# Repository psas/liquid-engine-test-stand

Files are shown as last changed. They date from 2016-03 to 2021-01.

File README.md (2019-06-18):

# liquid-engine-test-stand

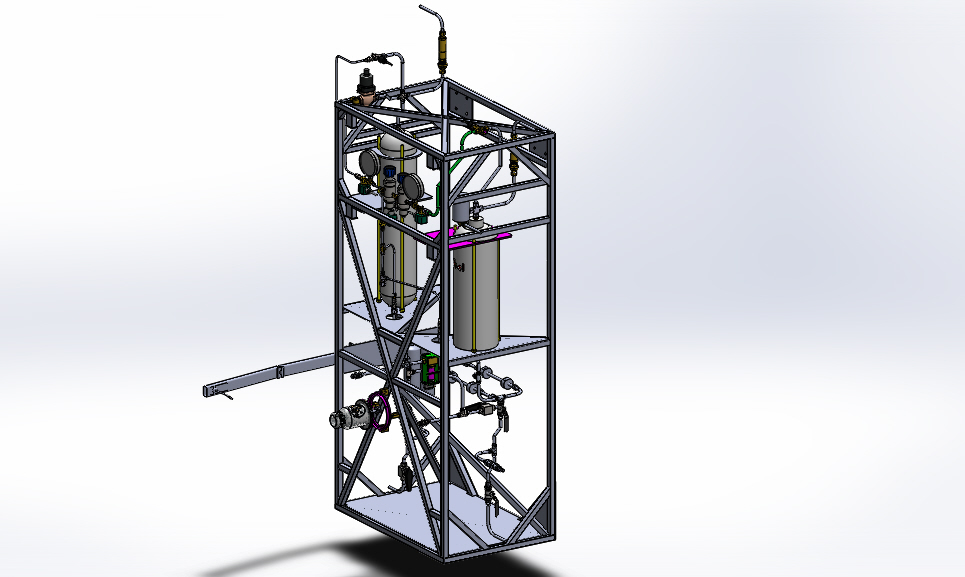
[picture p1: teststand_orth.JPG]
Orthographic View of Test Stand


# Liquid Fuel Engine Test Stand (LFETS) Project Overview

  PSAS team members have already designed and built a [2.5 kN regeneratively cooled bipropellant (liquid oxygen and ethanol) rocket engine](https://github.com/psas/liquid-engine-capstone-2015). This engine design included a number of innovative features including fully parametric CAD design using python scripts and SolidWorks, direct metal laser sintering (DMLS) additive manufacturing by i3D manufacturing, direct spark ignition and pintle injection. Although the rocket engine itself has already been produced, much of the overall system complexity lies in the piping, control, and data acquisition systems which support it. This project intends to flesh out these systems in order to test the engine and its successors.

  The test stand will safely test current and PSAS future generation liquid fuel engines prior to integration into a flight vehicle. PSAS will use the stand to measure engine performance, liquid fuel and oxidizer flow rates, propellant mixing capabilities and other engine performance figures of merit. These tests will be performed remotely, using automated valve switching and data acquisition systems. The LFETS system is designed to be portable by truck, and will support propulsion testing of engines up to 10 kN of thrust. The project will be open-source and will utilize live web-based Jupyter notebook design documentation.

  The feed system uses a classic regulated pressure-fed thermodynamic cycle. Gaseous nitrogen is the pressurant. The LFETS system includes a welded thrust loading truss structure, propellant and pressurant supply tanks, and feed system flow componentry. The project also includes safety and Failure Mode Effects Analysis, and procedures for safe operation and transport.
The LFETS Electrical Ground Support Equipment (EGSE) will allow for the test stand to be controlled remotely. The test stand computer controls all actuators in the LFETS system, auto-sequences engine ignition, start, shutdown, pad-safing, and contingency procedures for any test exception, as well as receiving telemetry from sensors and instrumentation. The LFETS EGSE system is derived from the 3rd generation [PSAS launch tower computer](https://github.com/psas/launch-tower), which uses a BeagleBone Black microcontroller, the [Marionette open-source DAQ](https://marionette-daq.github.io/), and a custom “SCADA-like” GUI.

## Useful Links

[CAD Files](https://github.com/psas/liquid-engine-test-stand/tree/master/cad/Test%20Stand%20CAD%20Files/current%20assembly)

[CAD Guide](https://github.com/psas/liquid-engine-test-stand/blob/master/cad/CAD%20Guide.pdf)

[Bill of Materials](https://drive.google.com/open?id=1SeBntyje6zpfy1jSxysdBP59IyhFcIg6SvVT6w5Bf4Y)

[PID](https://github.com/psas/liquid-engine-test-stand/tree/master/PID)

[Capstone Class Work](https://github.com/psas/liquid-engine-test-stand/tree/master/2018-2019%20Capstone%20documentation/Class%20papers%20and%20presentations)

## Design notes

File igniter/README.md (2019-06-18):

# Igniter for 2.2 kN Liquid Engine

Calculations have been acquired by inspecting the [2015 Liquid Engine Captsone](https://github.com/psas/liquid-engine-capstone-2015/blob/master/2kN/analysis/Jupyter_Notebooks/LFRE.ipynb)

Methods have been refined by interpretation of documents in the external_resources/ directory.

## UPDATES FROM 2019 CAPSTONE:

Igniter design documentation and validation can be found in the root folder under [Igniter-Design-Documentation.pdf](https://github.com/psas/liquid-engine-test-stand/blob/master/igniter/Igniter-Design-Documentation.pdf)  I would recommend starting with this document.

CAD for igniter arm can be found in the [Igniter Mockup CAD](https://github.com/psas/liquid-engine-test-stand/tree/master/igniter/Igniter%20Mockup%20CAD) folder.  The main assembly for the mockup is "Main Assembly.sldasm"

Momentum calculations for holding the arm in place can be found in the [calculations folder](https://github.com/psas/liquid-engine-test-stand/tree/master/igniter/Calcuations).

New Igniter BOM can be found in the PSAS Shared Drive, in the main [LFETS BOM](https://docs.google.com/spreadsheets/d/1SeBntyje6zpfy1jSxysdBP59IyhFcIg6SvVT6w5Bf4Y/edit?usp=sharing) document.

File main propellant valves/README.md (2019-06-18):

# Main Fuel and LOX Valves

The main pressurant valves consist of the main fuel valve and the main oxidizer valves.  The valves are control the flow of the Fuel and Oxidizer between the propellant tanks and the engine. The main fuel valve will be located on the fuel side of the test stand which carries Isopropyl alcohol. The main oxidizer valve will be located on the oxidizer side of the test stand which carries liquid oxygen.  The design requirements for each valve is that they be actuated remotely and able to work at pressures up to ~1000 psi. The LOX valve must also be able to work at cryogenic temperatures and be LOX compatible.

Several iterations of the main propellant valves have been worked on.

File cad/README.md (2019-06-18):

# Liquid Engine Test Stand CAD

  This section contains all the CAD models from previous and current version of the test stand made using Solidworks.
  
 ## Current Assembly
 
  This folder contains all the models for the current version of the test stand. The assembly for the test stand is labled LMTS_5. 
  
  Note: the entire folder must be downloaded in order to open the test stand assembly to load with all its components.
 
 ## Documentation
 
  ### CAD Guide
  
  This document contain information on all revisions, process, findings, and recommendations pertaining to constructing the test stand.
  
  ### Pipe Orders
  
  This folder contains folders and zip files that contain CAD drawings of pipes that have been or will be sent out for manufacturing.
  
 ## Previous Versions (from oldest to most recent)
 
  These folders contain previous versions of the test stand
  
  V.1
  test_stand_mods
  2016

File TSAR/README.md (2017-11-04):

# TSAR
Test Stand Automation and Regulation system for the Portland State Aerospace Society's (PSAS) Liquid fuel engine test stand.

## New Member Onboarding

If you are interested in joining the TSAR team, please reference 'Onboarding.pdf' in the root of this repository. 

## Definitions

LFETS - Liquid fuel engine test stand

Module - Valves, sensors, the engine, the igniter. Anything that is a single moving, sensing or functional unit.

## Test Stand Automation and Regulation System Overview

The TSAR group will build an embedded controls and data acquisition system (CDAQ) for a liquid fuel rocket engine test stand for the Portland State Aerospace Society. Solving this issue is vital because developing a liquid fuel rocket engine will decrease PSAS’s cost per launch drastically while also opening the door for considerably higher peak apogees. Without the development of a safe CDAQ solution for the test stand, PSAS cannot reach its goals. The TSAR solution is a student led, in house solution which will create a custom taylored, safety oriented soluton for test stand CDAQ. Our solution is unique because it will be entirely open-sourced with a focus on repeatability and simplicity to allow other amateur rocket groups to benefit from the liquid rocket engine technology. We will use an off-the-shelf Beagle Bone Black embedded computer and a Marionette DAQ board (a former PSU capstone) to implement this system and all software will be developed by the TSAR team of PSU undergraduates.

Project Contact: Mark Musil - Junior in Electrical Engineering at Portland State University (mmusil@pdx.edu)

## Key Requirements

The following aspects of the system are mandatory. More details are present in the document 'TSAR_Requirements.docx' in the root of this repository. The core features are:

1. Interactive graphical dashboard for state control
2. Safety and security of the entire system
3. Clean, thorough documentation of all group efforts including well-commented code, photographic and videographic artifacts, and thorough usage and debugging resources. 

#### What are the major deliverables?
A graphical front end with safety features. A nervous system of sensors and actuators with realtime data output from the RPi3 to the front-end.

#### How will we get to those deliverables and the deadline?

Divison of the project into: 

High level application design - GUI, interactive LFETS diagram, state control, security features, real-time data output, data storage

Mid-level system architecture - Discretization of the firing sequence into states, designation of states for each module.

Low-Level sensor specification and sensing - Specification of each sensor's range, and performance characteristics and interfacing of the sensors and actuatuators with the marionette/Rpi3.

#### What are the milestones we need to hit?
October: assessment of each High,mid,low system requirements and the tools which will be used for each system.
November: Completed state-machine design, Front end specifications completed, sensor specifications completed.
December: Interface with the fuel sensor or other LFETS needs and provide data output for their project.
January: All sensors specified, all valves under control.
February: Interface with all sensors and have real-time, time alligned data output.
March: 
April:
May: Hot fire :)
#### Are there dependencies that could impact the timeline?

It is important that we allign with the needs of the test stand team's needs. In addition, we need to begin delivering a part's list to the Beta project people. 

## Critical Objectives in Temporal Order (To-do list)

1. ### Pre-design
	1. Team Orientation
		1. General Training
			- [] GitHub
			- [] Python Notebook
			- [] System Overview
	2. Task Distribution
		1. Sensor Acquisition and Interfacing
		2. Actuator Acquisiton and Interfacing 
		3. Beagle Bone Black to Actuators
		4. Marionette To sensors
		5. System Design 
		6. Front-End and GUI
		7. Networking
		8. Record Keeping and Documentation
2. ### Design Stage
	1. Consult with Doug Hall concerning System Design
	2. Meet with Jacob Tiller about sensor requirements
	3. Investigate tools such as PyQT
	4. Brainstorm
	5. Determine Critical Path
3. ### Prototyping Stage 1
	1. Develop skeletal prototype of each sub system
		1. Minimal working set for interfacing
	2. Build sensor to screen prototype.

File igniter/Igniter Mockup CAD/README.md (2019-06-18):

# CAD guide

The top level assembly is "Main Assembly.sldasm"

The hinges on the igniter arm segments have changed a bit in the physical design, so as to minimize play.

This cad is mainly to be used as a mockup - not everything about the design is canon.

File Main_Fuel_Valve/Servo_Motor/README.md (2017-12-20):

# Main Fuel Valve

Servo Actuated Ball Valve

## To do:
  
  - [x] Design housing for servo, linkage, and valve
      - [x] Must maintain motor and valve-housing position against torque during action
        
      - [x] Must have sufficient clearance for physical linkage
      - [x] Print V.0 housing and test
     - [x] Make necessary updates for V.1 
        - [x] Print updated housing
        - [x] Post-process housing for assembly
    - [x] Acquire hardware & bits
    - [x] Assemble
- [x] Write Arduino code for pressure test
 - [ ] Acquire battery with sufficient amperage to operate valve
- [ ] Create test plan
        - [ ] determine all needed parts
        - [ ] acquire all needed parts
- [ ] Test valve with water at 1000 psi

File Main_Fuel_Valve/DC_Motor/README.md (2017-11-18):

# 12VDC Motor controlled Main Fuel Valve
<p align="center">
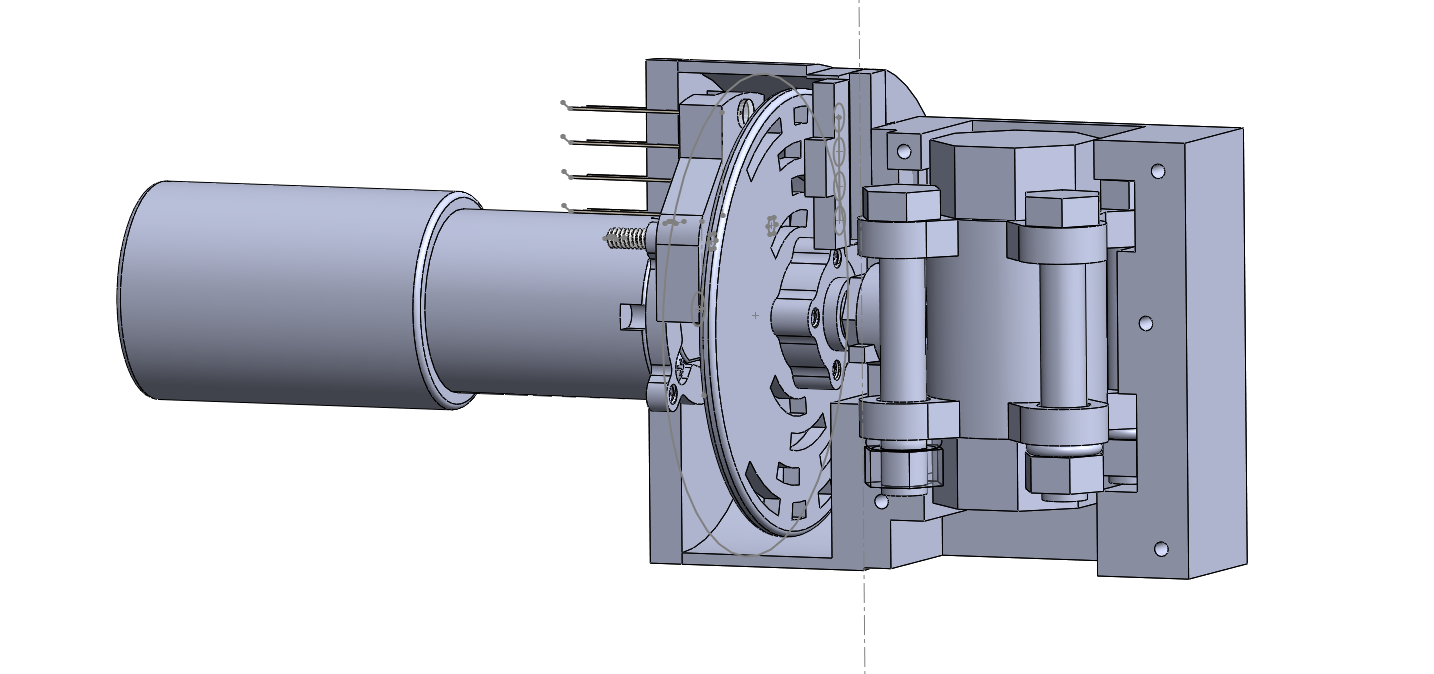
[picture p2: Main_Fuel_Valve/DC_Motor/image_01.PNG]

</p>

 DC Motor Valve control overview

   The 12VDC Motor Control project uses a very high torque planetary geared DC motor to crack, open, and close the main fuel valve. To control the position of the valve, a rotary encoding disk allows photo-sensors to receive light through concentric holes in the disk. The holes are designed to position the valve at shutoff, cracked from 0 to +60 degrees in 5 degree increments, and full open. The device is currently being controlled by an arduino.

###

## CAD Models
  
   The main assembly file is 12VDC_valve_assembly.SLDASM  
     
   PSAS authored files are:  
  
   12VDC_valve_assembly.SLDASM  
   Motor_12VDC_638263.SLDPRT - From drawing  
   Motor_12VDC_638263_shaft.SLDPRT - from drawing  
   Sensor_Head.SLDPRT  
   encoding_wheel.SLDPRT  
   Housing-Back.SLDPRT  
   Housing-Front.SLDPRT  

## Control

#### Basic Theory

The device uses Gray Code built into the encoding disk. The scheme is as follows: 

State - Code - Position

  00 - 0000 - detent (all)  
  01 - 0001 - closed  
  02 - 0011 - closed +5 dgrees  
  03 - 0010 - closed +10 degrees  
  04 - 0110 - closed +15 degrees  
  05 - 0111 - closed +20 degrees  
  06 - 0101 - closed +25 degrees  
  07 - 0100 - closed +30 degrees  
  08 - 1100 - closed +35 degrees  
  09 - 1101 - closed +40 degrees  
  10 - 1111 - closed +45 degrees  
  11 - 1110 - closed +50 degrees  
  12 - 1010 - closed +55 degrees  
  13 - 1011 - closed +60 degrees  
  14 - 1001 - Cracked <-> Open  
  15 - 1000 - Open (closed plus 90 degrees)  
  
  Detent position idicates an extreme condition. When a detent condition occurs, the script will determine the corrective action base on desired state.
  
  #### Control profiling
  
  Two control features requiring implementation are **Encoding Disk Interpolation** and **DC Motor Inertia Lag Profile**.
  
  **Encoding DIsk Interpolation**
      The source LED light is sensed by the photo-tranistors as the encoding wheel turns. At times the source LEDs will be partially occluded by the encoding wheel. The voltage throughput of the phototransistors will have a period of ramping up and ramping down due to this partial occlusion as the encoding wheel turns. If these ramping periods are profiled, a state can be identified more accurately than the 5 degree increments of the gray code. If these intermediate states can be proven accurate and reliable the encoding wheel should provide significantly improved resolution.
      
  **DC Motor Intertia Lag Profile**
      Due to the gearing and the inertia of the rotating mass in the motor, the motor continues to turn for a short time after it is switched off. This lag needs to be profiled so a switching point may be automatically determined based on desired state.
  
## To do:
  
  - [x] Design Motor to mount housing using jacob's design for the servo-motor as a base
    - [x] Must maintain motor and valve-housing position against torque during action
    - [x] Must have a mount for the "Sender" LED's (5mm) to provide bright light to the sensors
        - [ ] Bonus: Shield the "sender" and sensor heads from outside sources of light
    - [ ] Print the Housing front, back, LED Sender head, and photosensor head
        - [x] Initial printing of front, back, LED Sender head, and photosensor head
        - [ ] Print updated encoding wheel
        - [ ] Post-process housing front & back
    - [ ] Acquire hardware & bits
    - [ ] Assemble

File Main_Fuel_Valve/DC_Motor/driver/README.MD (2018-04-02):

# Code for the 12VDC motorized encoding valve project for LFETS.
### under construction

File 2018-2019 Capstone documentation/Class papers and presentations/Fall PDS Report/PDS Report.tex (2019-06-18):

% !TEX TS-program = pdflatex
% !TEX encoding = UTF-8 Unicode

% This is a simple template for a LaTeX document using the "article" class.
% See "book", "report", "letter" for other types of document.

\documentclass[11pt]{article} % use larger type; default would be 10pt
%\documentclass[twocolumn, 11pt]{article}  % will give a two column article with larger type
\usepackage{setspace} % lets you set the line spacing to single, 1.5 or double spaced. place after \maketitle
%\singlespace 
%\onehalfspace
%\doublespace

\usepackage[utf8]{inputenc} % set input encoding (not needed with XeLaTeX)

%%% Examples of Article customizations
% These packages are optional, depending whether you want the features they provide.
% See the LaTeX Companion or other references for full information.

%%% PAGE DIMENSIONS
\usepackage{geometry} % to change the page dimensions
\geometry{letterpaper} % or letterpaper (US) or a5paper or....
%\geometry{margin= 1in} % for example, change the margins to 2 inches all round
% \geometry{landscape} % set up the page for landscape
%   read geometry.pdf for detailed page layout information

\usepackage{graphicx} % support the \includegraphics command and options
\usepackage{float}
%\floatstyle{boxed} 
\restylefloat{figure}

%\listoffigures  % will give a list of figures
% \renewcommand{\figurename}{Example}  % changes it from figure to Example

%\usepackage{wrapfig} % will allow use of text wrapping around a figure
%\begin{wrapfigure}[lineheight]{position}[overhang]{width} would be used 
% r, l, i, o (right, left, inside edge, outside edge) (lower case is exactly here, upper case is float. for width use 0.5\textwidth for 1/2 of text width on the page

% \usepackage[parfill]{parskip} % Activate to begin paragraphs with an empty line rather than an indent

%%% PACKAGES
\usepackage{booktabs} % for much better looking tables
\usepackage{array} % for better arrays (eg matrices) in maths
\usepackage{paralist} % very flexible & customisable lists (eg. enumerate/itemize, etc.)
\usepackage{verbatim} % adds environment for commenting out blocks of text & for better verbatim
\usepackage{subfig} % make it possible to include more than one captioned figure/table in a single float
% These packages are all incorporated in the memoir class to one degree or another...

%%% HEADERS & FOOTERS
\usepackage{fancyhdr} % This should be set AFTER setting up the page geometry
\pagestyle{fancy} % options: empty , plain , fancy
\renewcommand{\headrulewidth}{0pt} % Gives a line at the top
\renewcommand{\footrulewidth}{0pt} % gives line at the bottom
\lhead{}\chead{}\rhead{} % puts stuff in the header
\lfoot{}\cfoot{\thepage}\rfoot{} % puts stuff in the footer

% \usepackage{lastpage}      % use this to have a x page of xx
%\cfoot{\thepage\ of \pageref{LastPage}} % this is the command for the center foot

%%% SECTION TITLE APPEARANCE
\usepackage{sectsty}
\allsectionsfont{\sffamily\mdseries\upshape} % (See the fntguide.pdf for font help)
% (This matches ConTeXt defaults)

%%% ToC (table of contents) APPEARANCE
\usepackage[nottoc,notlof,notlot]{tocbibind} % Put the bibliography in the ToC
\usepackage[titles,subfigure]{tocloft} % Alter the style of the Table of Contents
\renewcommand{\cftsecfont}{\rmfamily\mdseries\upshape}
\renewcommand{\cftsecpagefont}{\rmfamily\mdseries\upshape} % No bold!

\usepackage{amsmath} % allows use of \eqref{} to add () around referenced equations

%Outline format 
\renewcommand{\theenumi}{\Roman{enumi}. }
\renewcommand{\labelenumi}{\theenumi}

\renewcommand{\theenumii}{\Alph{enumii}. }
\renewcommand{\labelenumii}{\theenumii}

\renewcommand{\theenumiii}{\roman{enumiii}. }
\renewcommand{\labelenumiii}{\theenumiii}

\renewcommand{\theenumiv}{\alph{enumiv}) }
\renewcommand{\labelenumiv}{\theenumiv}

% Change the font size to something other than 10, 11, or 12 pt
%\usepackage{mathptmx}
%\usepackage{anyfontsize}
%\usepackage{t1enc}

%%% END Article customizations

%%% The "real" document content comes below...

%\title{Report Name} % alternate report title page
%\author{Jacob Tiller}
%\date{} % Activate to display a given date or no date (if empty),
         % otherwise the current date is printed 

\begin{document}
	% \fontsize{14}{16}\selectfont % Change font size, requires packages above
	\begin{titlepage}
		\centering
		%\includegraphics[width=0.15\textwidth]{imagename}\par\vspace{1cm}
		{\scshape\LARGE Product Design Specifications Report
\par}
		\vspace{.6in}
		{\huge\bfseries Liquid Propellant Engine: \par}
		\vspace{.2in}
		{\scshape\Large Test Stand Integration and Testing \par}
		\vspace{.75in}
		{\Large\itshape Bert DeChant \\ Sam Hasting Hauss \\ Peter Mazhnikov \\ Matthew Ng \\ Erik Potenza \\ Eric Thomas \\ Jacob Tiller \par}
		\vfill
		Capstone Adviser:\par
		Mark Weislogel

		\vfill

% Bottom of the page
		{\large \today\par}
\end{titlepage}

%\maketitle  % alternative make title with just author and report name stuff.
%\thispagestyle{fancy} 

\section{Purpose}

This document is intended to act as a guide for the development and testing of the Liquid Propellant Engine Test Stand. The Project Design Specification (PDS) will be used as the meter stick by which to ensure that all customer requirements are met and that the project is on track. 

\section{Project Background}
Portland State Aerospace Society (PSAS) is a collection of students, citizen-engineers and industry mentors with a long history of developing low-cost, open-source rocket hardware and avionics systems. In 2018 PSAS joined the Base 11 Space Challenge (Base 11),  a competition for student university groups to produce and launch a liquid-propelled single stage rocket to 100km. In line with PSAS’ vision statement, the challenge acts as an additional incentive to build and launch the next PSAS launch vehicle, Launch Vehicle 4 (LV4). Prior to the design and construction of LV4, the rocket’s liquid bi-propellant rocket engine must be tested.

PSAS is preparing to test a 2.2 kN regeneratively cooled bipropellant (liquid oxygen and isopropanol) rocket engine. This engine design has a number of innovative features including fully parametric CAD design using Python and SolidWorks, direct metal laser sintering (DMLS) production by i3D manufacturing, augmented spark torch ignition and pintle injection.

The Liquid Propellent Engine Test Stand was originally produced by a Portland State University capstone team in 2015. The team designed, analyzed, and constructed the frame of the test stand and set in path many of the construction elements. Since the frame was constructed, the stand has been awaiting final integration and installation of some subsystems including propellant and cryogenic plumbing as well as the engine mounting \& interfacing. 

PSAS has asked our team to complete the construction of the test stand and test the 2.2kN engine. Upon completion, the test stand will continue to serve the organization by testing the liquid-oxygen electric feed system, cryogenic composite oxidizer and propellant tanks, and the next generation 8kN rocket engine. Our work will synergize with the efforts of previous capstone teams to prototype the technology for LV4 and to compete in the Base 11 Space Challenge.

\section{Mission Statement}
The proposed project is to integrate, test, and analyze our prototype engine.  An analysis of the first static test fire is scheduled to be accomplished in the spring of 2019.

We will integrate and test the previously designed engine and validate its performance metrics including thrust, cooling capabilities, and chamber pressures. Engine testing will be conducted in a reproducible manner according to a written standard operating procedure which will emphasize safe operation. Other procedures for interacting with authorities, safety, and testing site hazard analysis will be written and used during this project. The captured data from the static fires and the analysis methods will be published under an open-source license.

The test stand needs to stand up to the rigors of testing a rocket engine while also incorporating safety and data acquisition capabilities.  Furthermore, it needs to have the ability to be used with multiple sizes of engines, although only the 2.2kN engine will be tested in the Spring of 2019.

An analysis will be conducted to determine engine performance. Data will be acquired through a Data Acquisition system (DAQ) working under the Test Stand Automation \& Regulation system (TSAR). TSAR will act primarily as a safety and management tool to provide safeguards for both human and system operations.  Upon completion of initial testing, the data acquired will be compared against the engine’s theoretical performance characteristics. Analysis tools include Solidworks, Python programs such as Jupyter Notebooks, and GitHub for collaboration. The data analysis will determine the viability of testing the future generation 8kN engine. The analysis will also prepare PSAS for integration of the liquid engine into the flight-ready control system of future rocket designs to be used in the Base 11 Challenge.

Standard Operating Procedures will be formalized to meet or exceed industry standards as to mitigate risk towards personnel, equipment, and property. All documentation will be created in accordance with relevant industry standards and best practices determined useful by PSAS. All documentation will contain sufficient detail, background information, and operational description to enable a smooth transfer of knowledge to new project members.

\section{Top Level Project Plan}

Project completion will include integration, testing, and analysis of the 2.2kN engine. The project outcomes will be an analysis of the first static test fire, which is scheduled to be accomplished in the spring of 2019, along with the other project deliverables listed below:

\begin{itemize}
\item Post-processing 3D printed engine
\item Jig creation, precision machining, and CT scanning analysis
\item Integrated assembly (including structures, electronic ground support equipment, and plumbing)
\item Control and data acquisition software and design documentation
\item Operational, and transport procedures
\item Failure Effects Mode Analysis (FMEA), House of quality, and system safety analysis
\item Leak, hydro, and system proof testing buy-offs
\item Integrated cold-flow test data, including the engine injector
\item Hot fire test data for the 1.0 version 3D printed engine
\end{itemize}

\begin{figure}[H] % h - place here; t - top of page; b - bottom; p - put on floats only page; ! override parameters, H - place exactly here
\centering
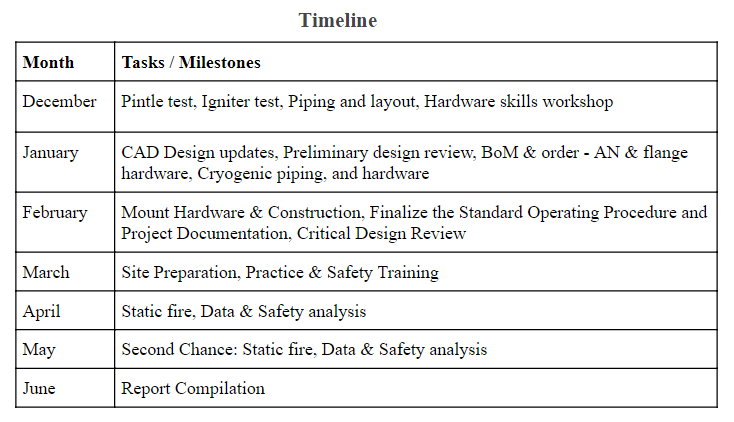
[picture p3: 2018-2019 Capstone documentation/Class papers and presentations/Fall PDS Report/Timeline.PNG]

\caption{Project Timeline \label{fig:timeline}}
\end{figure}

\section{Customers and Stakeholders}

Portland State Aerospace Society - Andrew Greenberg
Capstone Advisor - Mark Weislogel
Capstone Class - Sung Yi / Faryar  
Base 11
Oregon Space Grant Consortium - Catherine Lanier 

\subsection{Customer Interviews and Feedback}

Customer feedback per project customer. 
The main bullet is the project customer and the sub-bullets are the requirements. 

\textit{PSAS:}
Interview Question: What kind of documentation do we need?
\begin{itemize}
\item Create a formal failure mode and effect analysis document
\item Create a Standard Operating Procedure Manual
\item Create a post-firing analysis of engine with suggestions
\item Create a background, research, and theory of operation document
\item Create training materials
\item Create documents for system maintenance
\item Create documents for test site management
\item Create documents for the transportation of the test stand and propellants
\item Create a SolidWorks CAD model of test stand assembly
\item Regularly send all technical documents and files to Github
\item All other tests stand administrative files to be stored on PSAS shared google drive
\item Create a bill of materials
\end{itemize}

Interview Question: What safety standards must be met?
\begin{itemize}
\item Safety procedures are known and followed
\item Participation in any mandatory safety training
\item Human interaction withstand during test must be minimized
\item No person(s) is to approach the test stand while the system is pressurized
\item Redundant systems must be implemented to prevent accidental pressurization of the system
\end{itemize}

Interview Question: What will be needed for the system?
\begin{itemize}
\item Isopropyl alcohol will be the fuel
\item Liquid oxygen will be the oxidizer
\item Nitrogen gas will be the pressurant
\item Data acquisition equipment from TSAR
\item 2.2 kN engine from PSAS
\item Fully constructed test stand
\end{itemize}

Interview Question: What data will we need to acquire?
\begin{itemize}
\item Engine chamber pressure
\item Fuel mass flow rate
\item Propellant mass flow rate
\item Injector spray angle
\end{itemize}

\textit{Capstone Adviser:}
Interview Question: What are your goals for meetings?
\begin{itemize}
\item Bi-weekly meetings to discuss project and progress
\end{itemize}

\textit{Capstone Class:}
Interview Question: What documents must be submitted?
\begin{itemize}
\item Create a Project design specification report
\end{itemize}

\section{Product Design Specifications (PDS)}

\begin{figure}[H] % h - place here; t - top of page; b - bottom; p - put on floats only page; ! override parameters, H - place exactly here
\centering
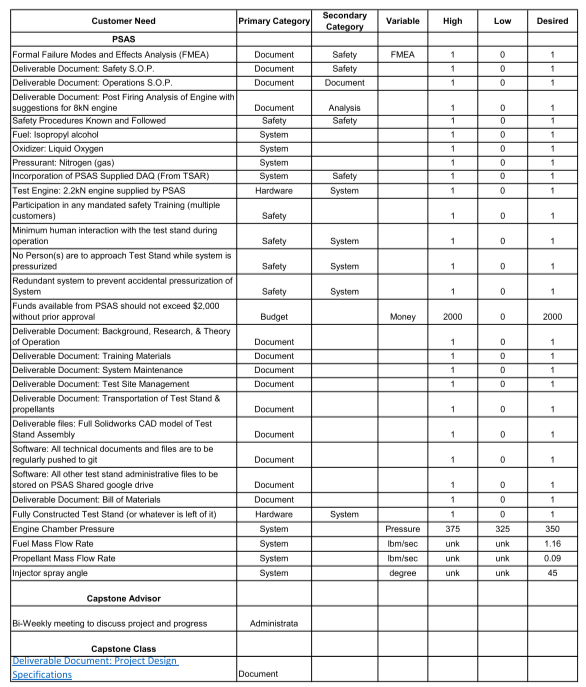
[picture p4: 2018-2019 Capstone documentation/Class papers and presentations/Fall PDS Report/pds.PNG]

\caption{Project Design Specifications \label{fig:PDS}}
\end{figure}

\section{House of Quality}

\begin{figure}[H] % h - place here; t - top of page; b - bottom; p - put on floats only page; ! override parameters, H - place exactly here
\centering
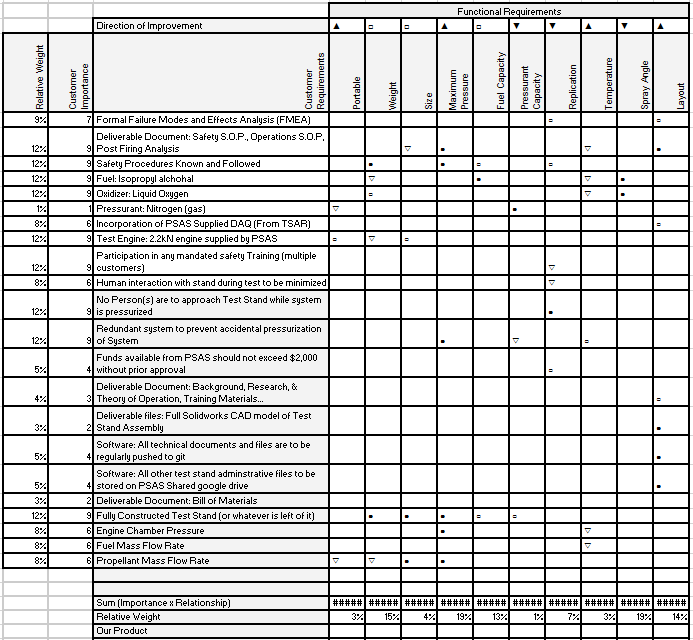
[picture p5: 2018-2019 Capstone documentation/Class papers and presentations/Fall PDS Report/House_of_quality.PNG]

\caption{House of Quality \label{fig:PDS}}
\end{figure}

\section{Conclusion}

A 2.2kN engine supplied by the Portland State Aerospace Society is to be tested using the Liquid Propellant Engine Test Stand. The capstone team is tasked with the integration of some subsystems and components including the engine into the test stand. The team is further tasked with executing a static fire of the stand to acquire engine performance data.

The most important requirements of this project are those related to safety. The team expects to apply significant effort in the creation, practice, and delivery of safety documentation. PSAS requires the highest level of safety and care to be maintained through all phases of integration and operation.

A particularly difficult requirement is the minimization of human interaction. Fuel and oxidizer loading will have minimum human interaction with the test stand. Implementing computerized systems will be an educational experience for the team. It may pose a hurdle as the team has little to no experience with robotic systems.

The team is excited to learn from the integration and static firing of the engine. We anticipate several hurdles in this project but are excited to meet challenges with creative designs and to meet the requirements of PSAS and MCECS Capstone.

\end{document}

%[appendix]
%\appendix
%\clearpage
%\pagenumbering{roman}
%\section{Appendix}

% [Helpful stuff]
%\newpage
%\section{}
%\subsection{}
%\subsubsection{}
%\paragraph{}
%\subparagraph{}

% [Text sizes] 
%{\tiny tiny words} tiny words
%{\scriptsize scriptsize words} scriptsize words
%{\footnotesize footnotesize words} footnotesize words
%{\small small words} small words
%{\normalsize normalsize words} normalsize words
%{\large large words} large words
%{\Large Large words} Large words
%{\LARGE LARGE words} LARGE words
%{\huge huge words} huge words

%[Test styles]
%\textit{words in italics} words in italics
%\textsl{words slanted} words slanted
%\textsc{words in smallcaps} words in smallcaps
%\textbf{words in bold} words in bold
%\texttt{words in teletype} words in teletype
%\textsf{sans serif words} sans serif words
%\textrm{roman words} roman words
%\underline{underlined words} underlined words

% [Lists]
%\begin{enumerate}
%\item First thing
%\item Second thing
%\begin{itemize}
%\item A sub-thing
%\item Another sub-thing
%\end{itemize}
%\item Third thing
%\end{enumerate}

% [Figures and Tables]
% [website for floats and captions]
% https://en.wikibooks.org/wiki/LaTeX/Floats,_Figures_and_Captions 

%\begin{figure}[placement specifier] % h - place here; t - top of page; b - bottom; p - put on floats only page; ! override parameters, H - place exactly here
%\centering
%\includegraphics[width=0.5\textwidth]{filename}
%\caption{ text here \label{fig:marker}}
%\end{figure}

%figure~\ref{fig:marker}

%\begin{table}
%  \centering
%    \begin{tabular}{| l c r |}
%    \hline
%    1 & 2 & 3 \\
%    4 & 5 & 6 \\
%    7 & 8 & 9 \\
%    \hline
%\cline{1-2} column#-column#
%\cline{2-3} column#-column#
%    \end{tabular}
%  \caption{A simple table \label{tab:marker}}
%\end{table}

%table~\ref{tab:marker}

%\begin{equation} \label{eq:marker}
% equation
%\end{equation}

%\eqref{eq:marker}

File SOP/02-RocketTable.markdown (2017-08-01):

---
title: SSH In to Flight Computer Test
layout: base
---

# Rocket table setup

## Common Setup
Start with the Avionics Stack on the rocket cart and batteries charged

 1. Make sure there is something attached to the wifi radio connector (SMA at the top of the Avionics Stack)
    - Either the antenna or a load
 1. Plug in table
 1. Turn on LTC Power brick
 1. Switch on launch tower computer main power
    - Wait a few seconds, verify lights: four reds, blinking blue, blinking green
 1. Visually verify umbilical cord is plugged into the avionics module

## Connect to wifi

 1. Turn on ground control router
 1. Connect to `psas` wifi network
    - Password will be written on the AP or the table

## Verify LTC

 1. `ping ltc`
    - `ltc` should be in the DNS offered via DHCP

## Get flight computer going

 1. Power on Avionics Stack
    - On off switch on battery cable
 1. `ping 10.10.10.5`
    - Actually talking to the RocketNet Hub
 1. Connect to [commander](https://github.com/psas/commander) running on the nuc from  your laptop.
    - Open a browser to <http://ground.psas.lan:5000/>

## In commander
 1. RNH tab -> click "[1] FC On"
    - Click only this, nothing else!
    - Wait for flight computer to boot and establish networking (about 40 seconds? ping 10.10.10.10)
 1. Boot up other services
    - Do *NOT* click "[6] Wifi PA On"
    - Click other on buttons and verify blinky lights for each board
    - You can turn on RasPiCam 2, but the camera is attached to the air frame so it may be a little dull.
 1. Default tab
    - Verify versions of major subsystems by clicking on each button under the "Versions" header

## At laptop
 1. `ssh root@10.10.10.10`
    - Actually talking to Flight Computer
    - See note on wood base of avionics stack for password

## Turning on the RasPiCams
 1. Still on the RNH tab -> click "[2] RasPiCam 1 On"
    - Verify the bottom-most green board starts blinking yellow and green
    - `ping 10.10.10.50` or `ping 10.10.10.60`
 1. `ssh pi@10.10.10.50` or `ssh pi@10.10.10.60` based on which RasPi you're trying to get to
    - Use the usual password

## Common Shutdown
 1. Cleanly shut down the Flight Computer
    - `shutdown now`
    - Wait for FC to shut down (about 30 seconds?  Or 5(?) seconds after it stops responding to pings.)
 1. Using commander: click FC Off (Green button)
    - Green light on computer will go out
 1. Using commander: click All Off
 1. Switch off Avionics Stack
    - On off switch on battery cable
 1. Switch off Launch Tower Computer main power
    - Red switch on side of LTC case
 1. Turn off LTC Power brick
 1. Disconnect laptop from `psas` wifi network
 1. Turn off ground control router.
 1. Unplug table

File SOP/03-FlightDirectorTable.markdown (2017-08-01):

---
title: Seting up the flight director table
layout: base
---

# Flight director table setup

## Starting up the flight director table

1. Plug it in to the wall
1. Switch on the surge protector
1. Check for blinking lights on the router
1. Turn on the NUC (bottom slider shelf, silver button on top)
1. Login as root, pass on the sticky

## Start up the launch tower computer

1. Setup LTC {link to other procedure book}

## Boot up Kivi on the flight director table

1. Open terminal
1. `cd psas/launch-tower-comm/launch-tower-comm`
1. `./ltc.py`
1. Verify that the upper right says "Nominal"
1. Play with the LTC to your heart's content

## Boot Commander on the flight director table

1. New terminal tab
1. `cd psas/commander`
1. `python app.py` to run in debug mode. Then you can point your laptop at the NUC directly

## Bring up the flight computer

1. {link again to other procedure book}

## Bring up telemetry

1. New terminal tab
1. `cd psas/telemetry`
1. `./telemetry.py`
1. <http://ground.psas.lan:8080/>

### Getting the trackmaster running

1. `ssh root@10.10.10.10` (password on the base of the avionics stack)
1. `./startFC`
  1. It should give you a happy message

### Start up the trackmaster

1. Check that the lan and PoE cables are correctly installed
  1. LAN goes to router (NOT THE POE CABLE!)
  1. POE cable goisg to the black box on the trackmaster
1. Plug in the cable labeled POE
  1. Green light on the black box
  1. A little later a blue blinky light on the clear box
  1. Green light on the board by the antenna
1. Data should be coming in to ground.psas.lan

## Getting video from the raspicams

1. Get the flight computer running via Commander
1. Boot up raspicam1 from Commander
1. Make sure the trackmaster is running
1. Open VLC on your laptop and connect to `rtsp://10.0.0.3:8554/`

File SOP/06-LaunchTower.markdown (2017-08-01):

---
title: Launch Tower Setup
layout: base
---

# Launch Tower Setup

Overview:

With the exception of a impact wrench or angle drill, this should be a tool-less setup. If you think you need to use a tool, look for the labels on the tower.

## Materials
 - 3 Sand Screws
 - 3 Tower sections
 - 3 ratchet straps
 - Umbilica Bar
 - Antenna Bar
 - Launch Rail
 - Antenna bar adjustment bar
 - One small stake
 - Impact wrench or right angle drill.

## Setup

 1. Lay tower sections on the ground, aligining the 'rail up' labels so they are all going the same direction.
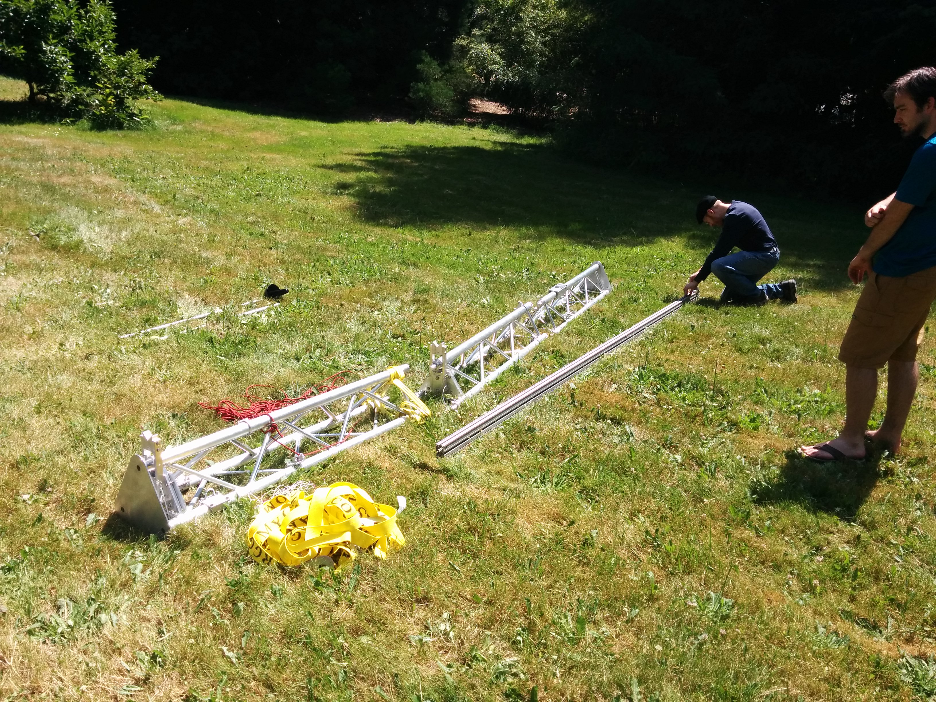
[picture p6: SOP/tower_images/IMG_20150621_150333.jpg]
Launch Tower Setup
    
 1. Connect the sections of the tower, placing the 3 tapered pins into the respective holes and inserting the retainer snap that is attached to the string below.
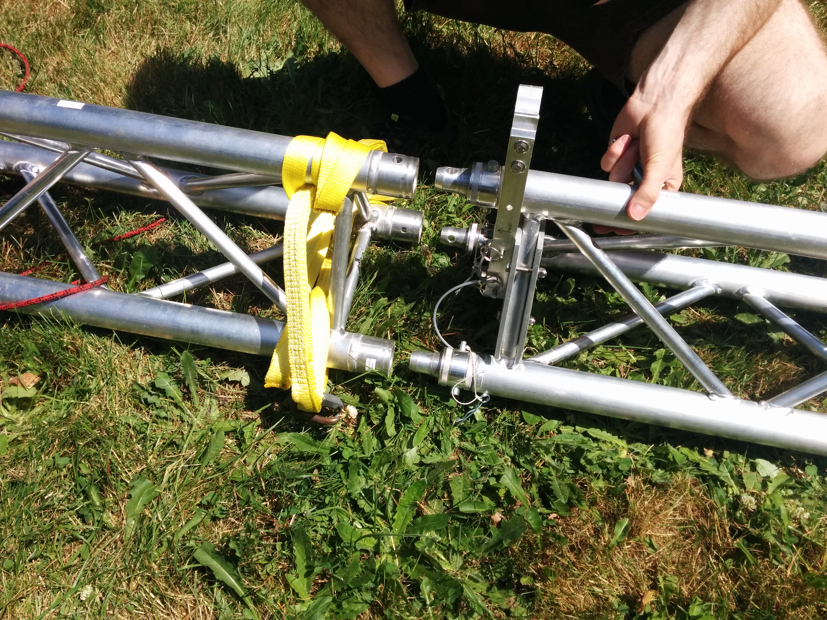
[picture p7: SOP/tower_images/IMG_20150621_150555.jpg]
Launch Tower Setup
    
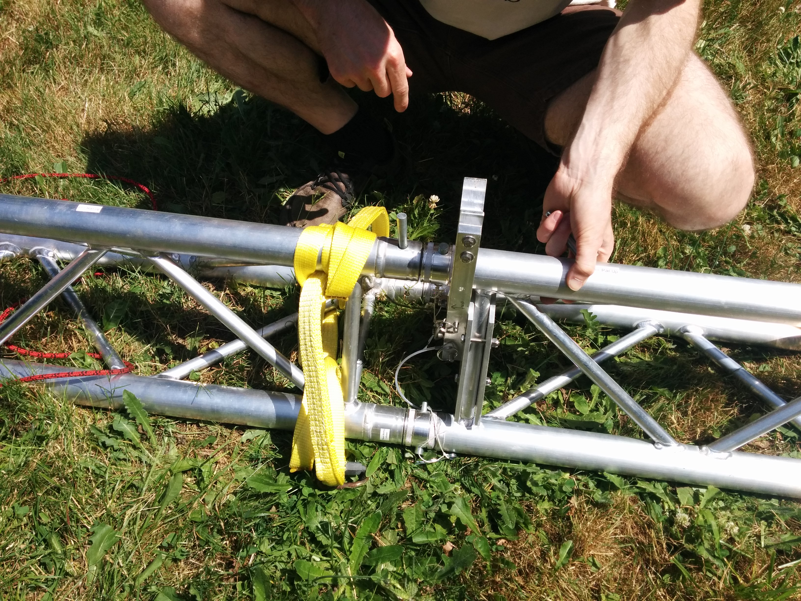
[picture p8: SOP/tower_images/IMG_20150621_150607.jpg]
Launch Tower Setup
    
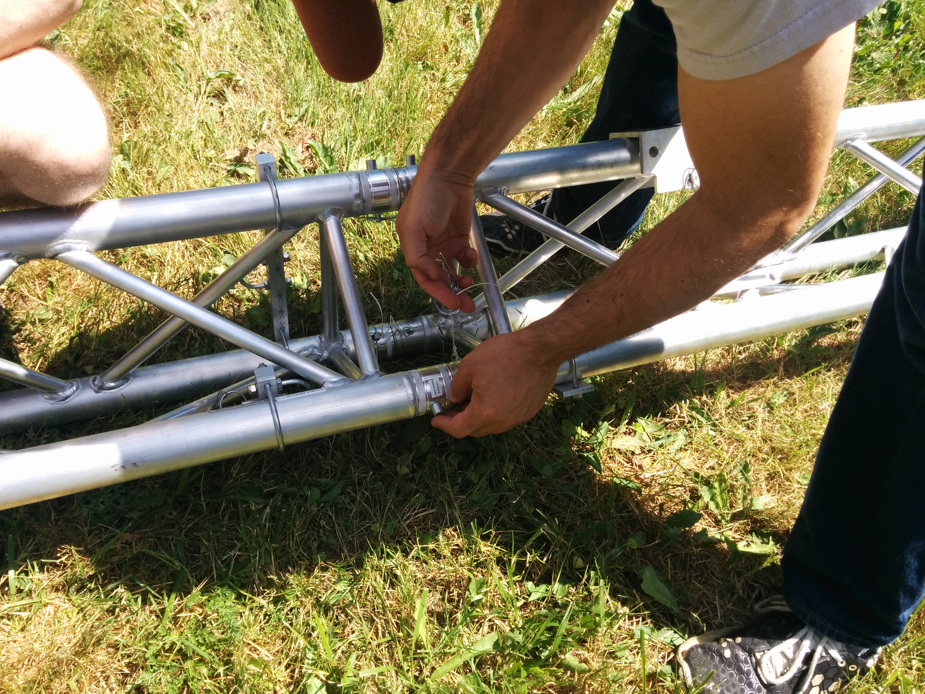
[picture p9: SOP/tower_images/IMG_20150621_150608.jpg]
Launch Tower Setup
    
 1. Pull the rope and quick link down to the lower section of the tower and affix it to a cross bar.
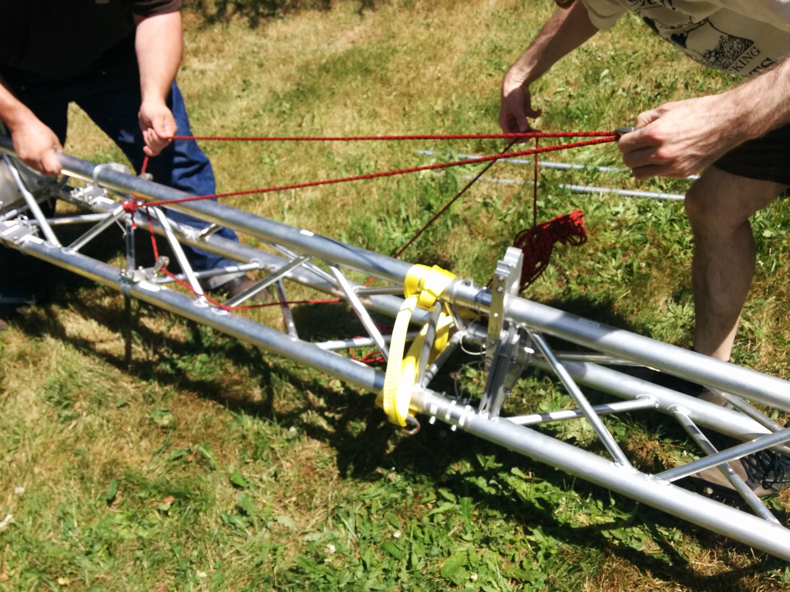
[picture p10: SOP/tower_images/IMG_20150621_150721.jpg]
Launch Tower Setup
    
 1. Connect the hooks of the ratchet straps to the quick links on the upper section of the tower.
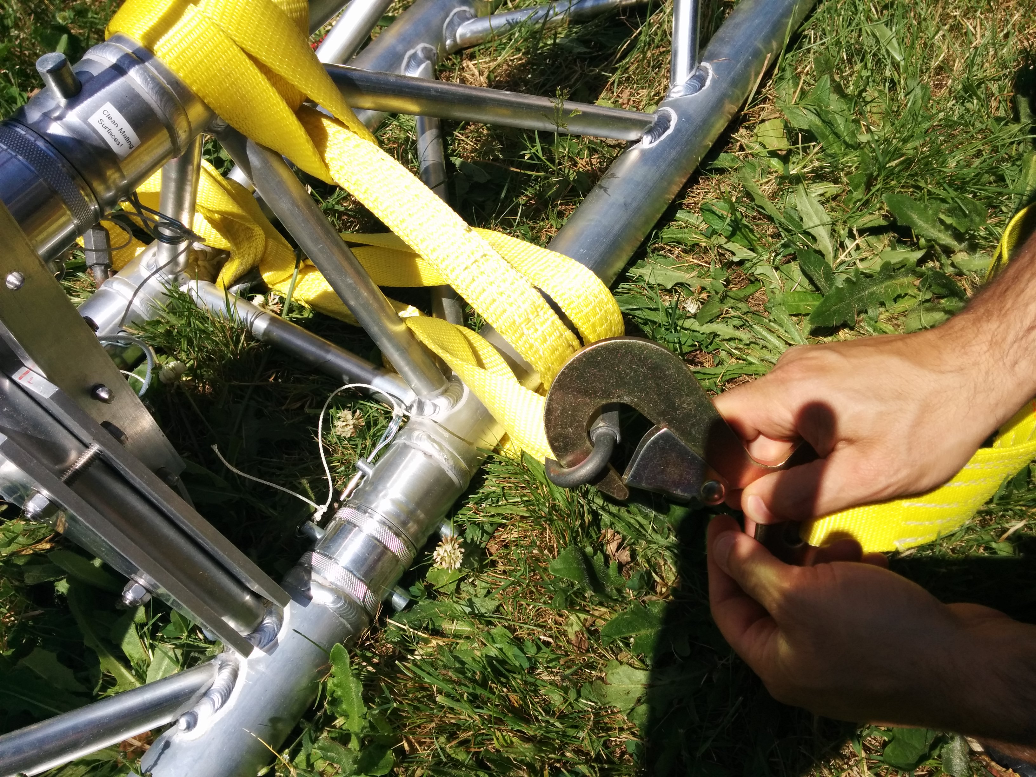
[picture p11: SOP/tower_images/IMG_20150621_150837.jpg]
Launch Tower Setup
    
 1. For the upper and mid sections, install the rail V-guides by removeing the 2 quick pins, and rotating the V-guide 180 degrees, and re-installing the two quick pins.
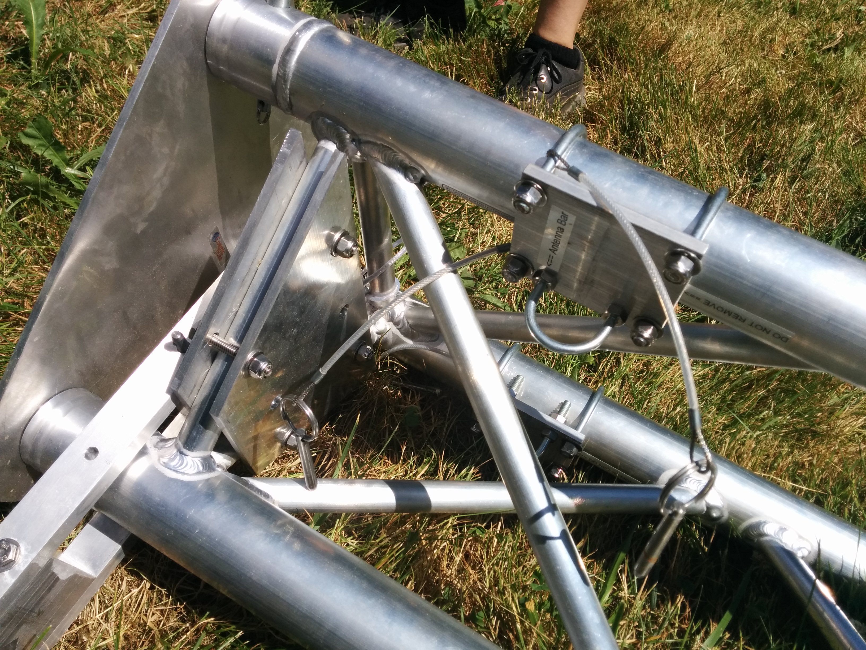
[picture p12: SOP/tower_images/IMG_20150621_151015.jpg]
Launch Tower Setup
    
 1. Slide the antenna bar thru the 2 u-bolts at the top of the tower, such that the slot in the end of the antenna bar is on the side of the u-bolts that has 2 quick pins. Take 2 of the quick pins and place them thru the antenna bar such that it won't slide laterally. (there will be 1 quick pin dangling)
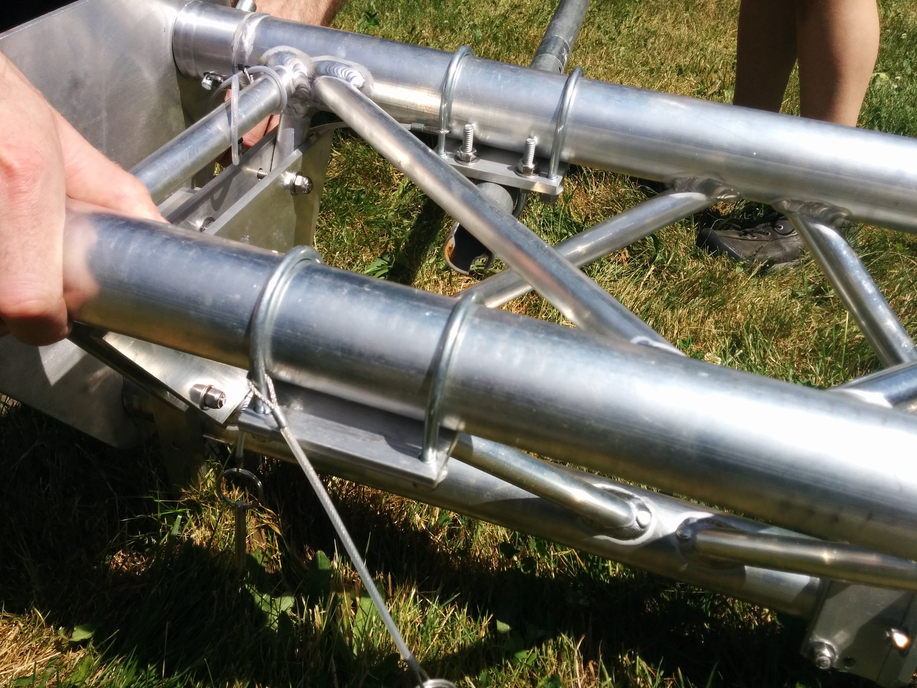
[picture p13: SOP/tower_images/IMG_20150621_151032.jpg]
Launch Tower Setup
    
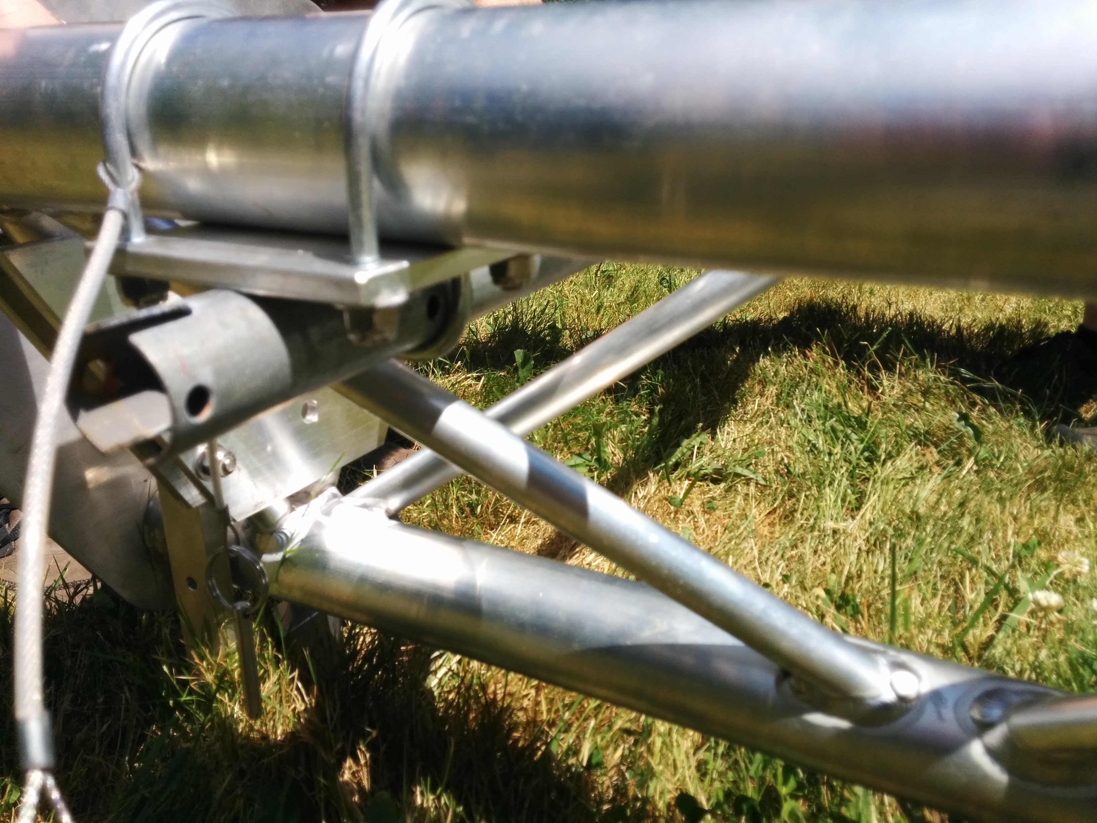
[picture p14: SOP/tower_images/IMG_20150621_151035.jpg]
Launch Tower Setup
    
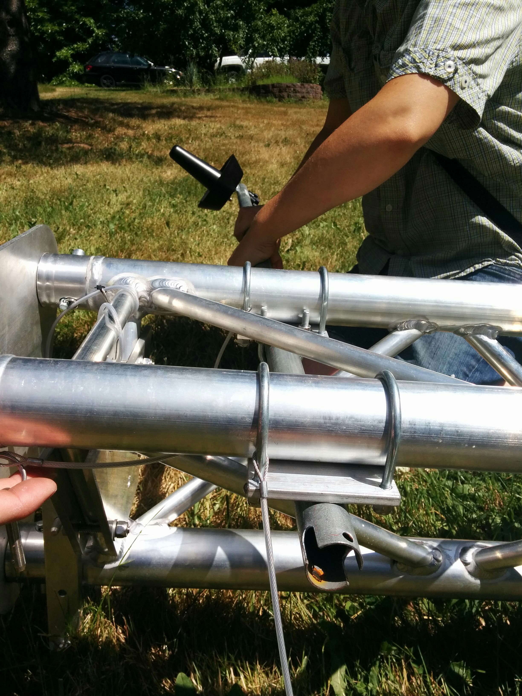
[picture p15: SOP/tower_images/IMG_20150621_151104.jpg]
Launch Tower Setup
    
 1. Install the antenna angle adjustment bar by sliding it in the slot at the end of the antenna bar and inserting the quick pin to retain it.
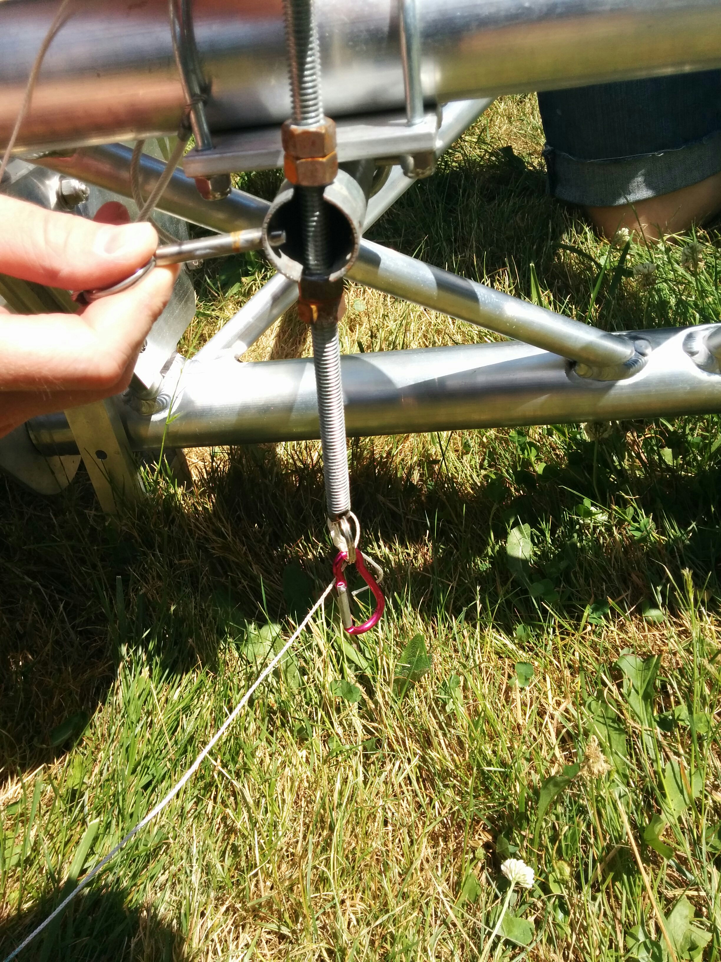
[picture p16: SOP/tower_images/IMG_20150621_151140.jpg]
Launch Tower Setup
    
 1. Rais the tower verticall with one person to hold it in place.
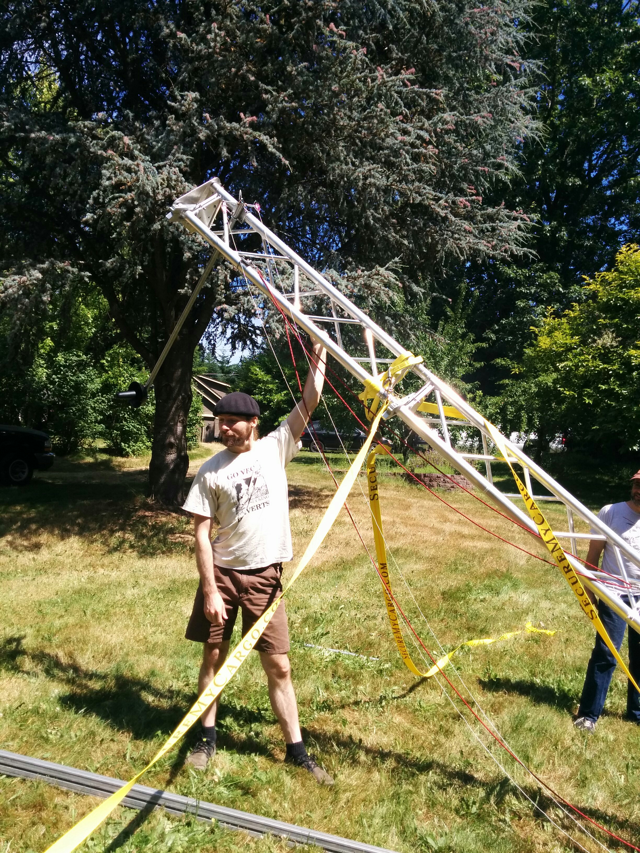
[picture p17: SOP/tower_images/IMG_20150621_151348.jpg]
Launch Tower Setup
    
 1. Using appropiate power tool, drive sand screws into the ground at 120 degrees from each other, with the ratchet straps slightly taunt. If the power tool has insufficient torque to drive in the sand screw, use an 18 inch breaker bar.
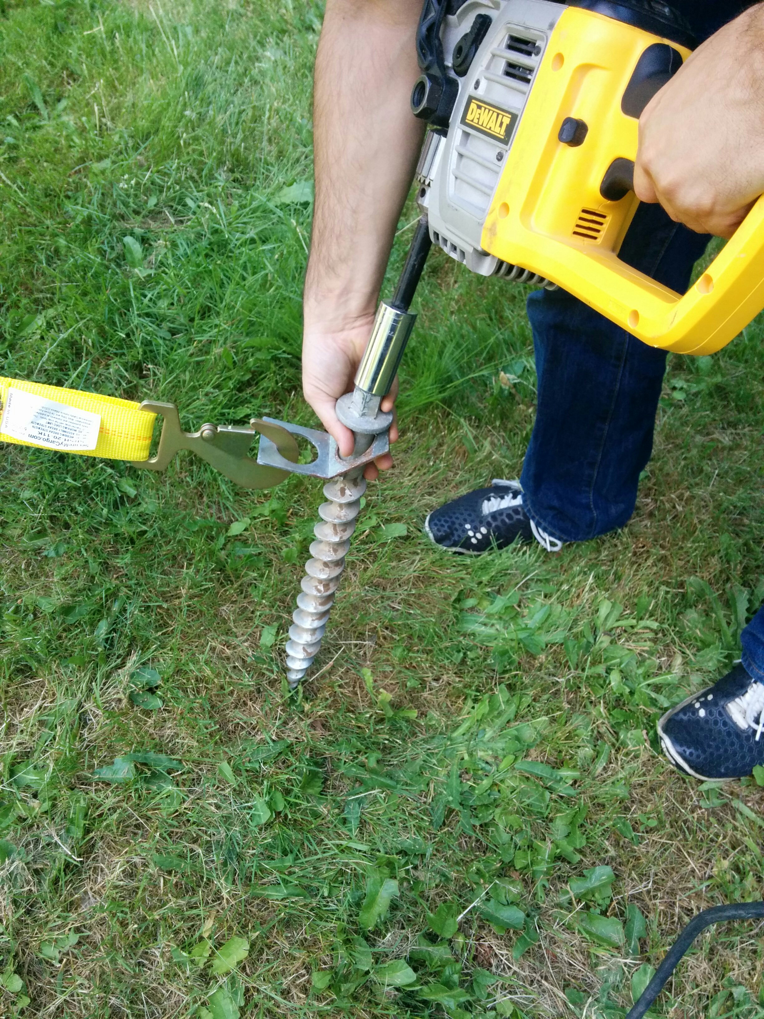
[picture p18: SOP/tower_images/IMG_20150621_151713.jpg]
Launch Tower Setup
    
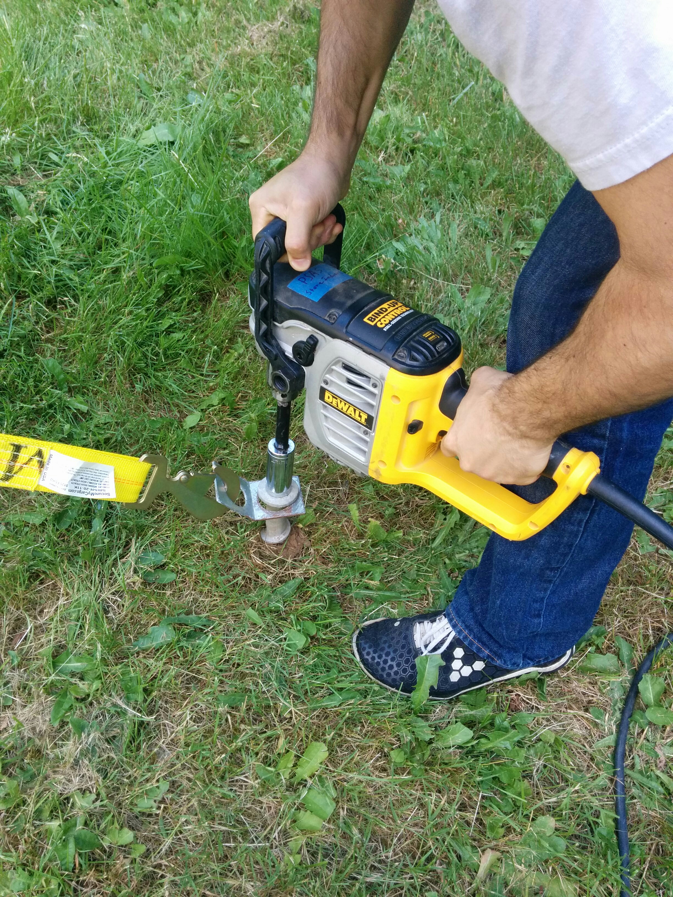
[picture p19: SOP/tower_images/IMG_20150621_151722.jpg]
Launch Tower Setup
    
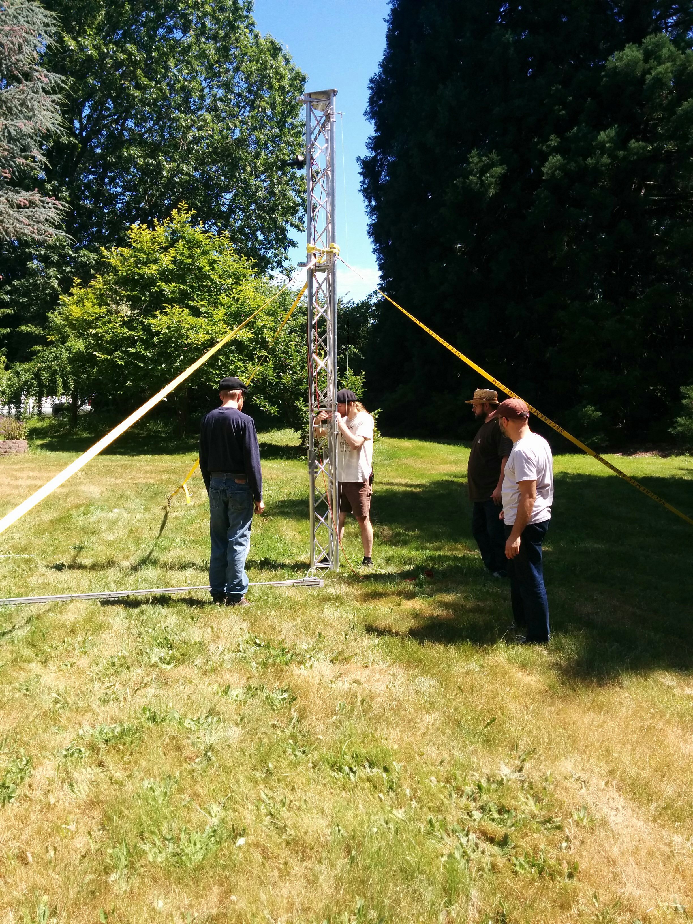
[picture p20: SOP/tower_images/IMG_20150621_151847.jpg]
Launch Tower Setup
    
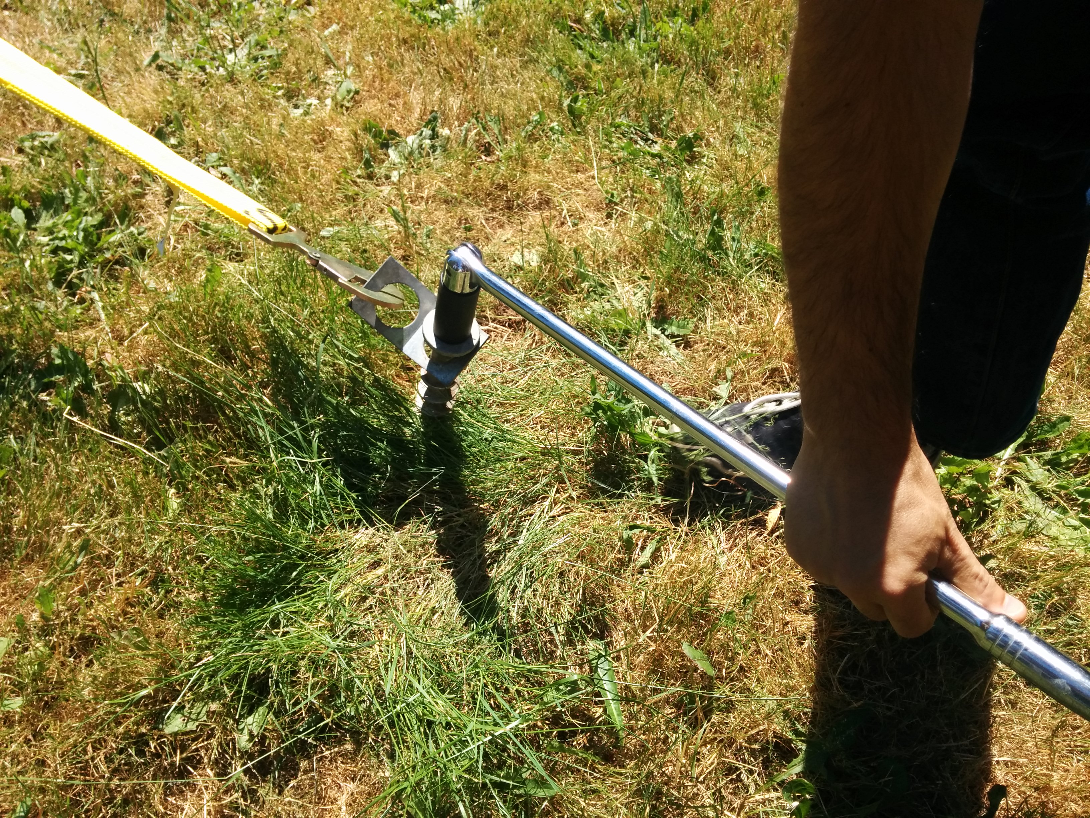
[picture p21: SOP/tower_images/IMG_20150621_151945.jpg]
Launch Tower Setup
    
 1. Remove the foot mount quick pin, pivot the mount down, and install the quick pin in the lower back block.
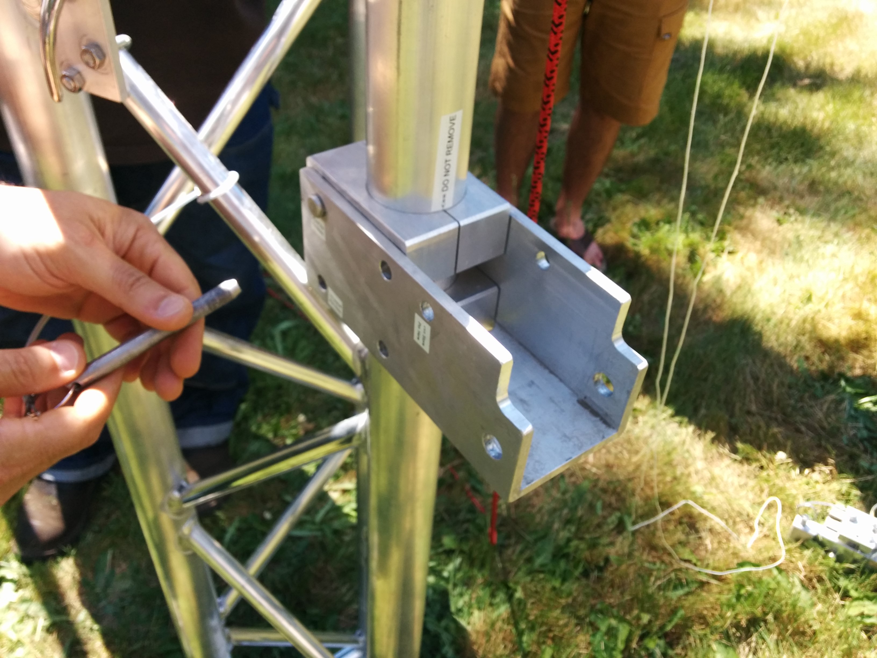
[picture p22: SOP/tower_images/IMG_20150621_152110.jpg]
Launch Tower Setup
    
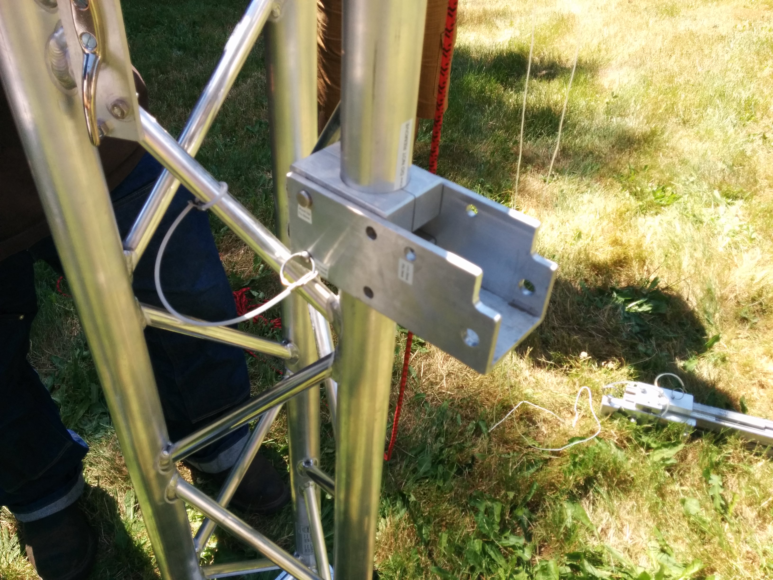
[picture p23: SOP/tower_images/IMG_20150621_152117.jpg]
Launch Tower Setup
    
 1. Slide the foot of the rail into the mount, and install the 1/2 inch quick pin to connect the rail to the tower.
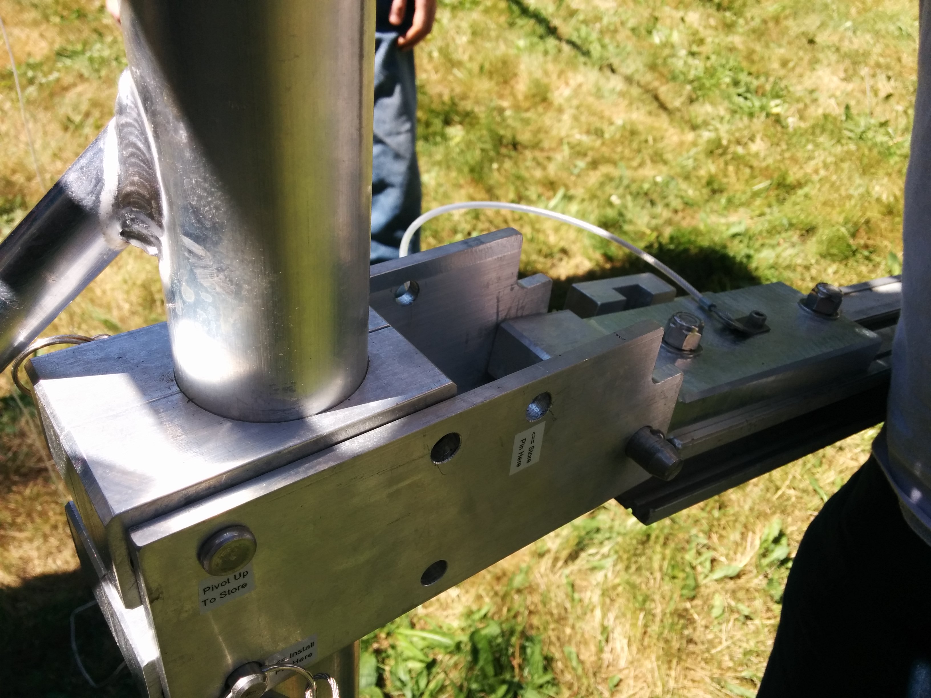
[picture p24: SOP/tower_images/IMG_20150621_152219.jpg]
Launch Tower Setup
    
 1. Connect the quick-link from the rope to the D-ring on the back side of the rail, then raise the rail and tie it off.
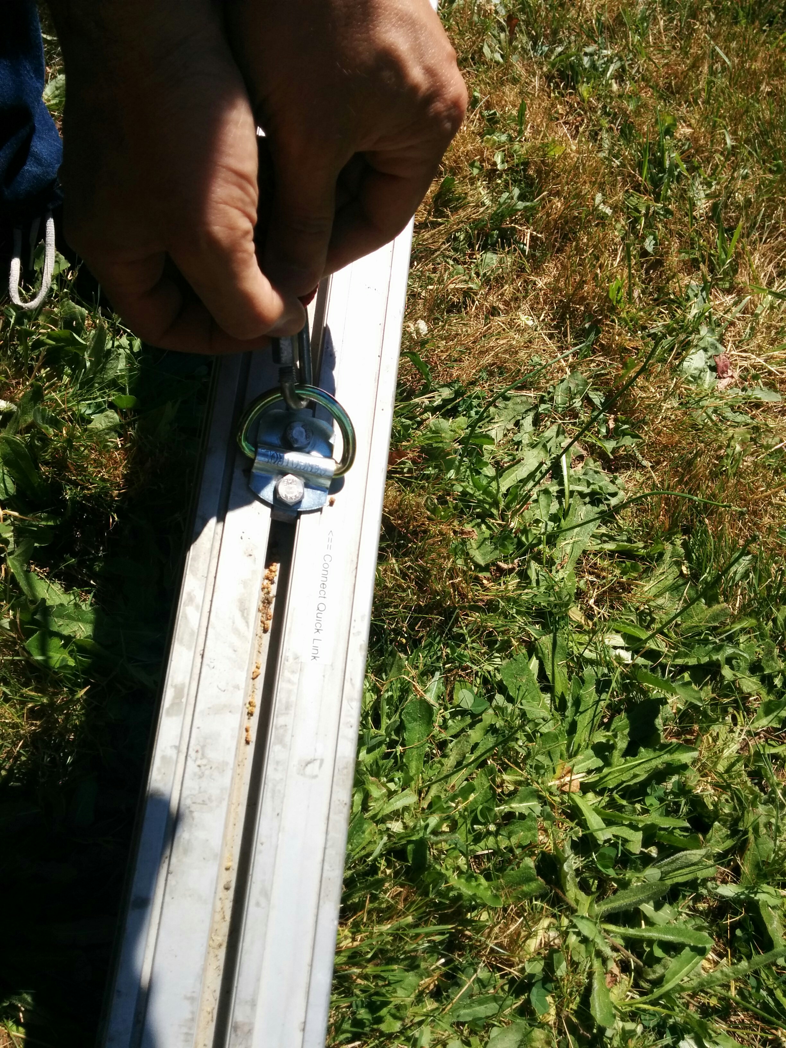
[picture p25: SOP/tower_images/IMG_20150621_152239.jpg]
Launch Tower Setup
    
    Launch Tower Setup
    Launch Tower Setup
    Launch Tower Setup
 1. Remove the foot from the storage block, and slide it in the front of the foot block, and re-pin in place.
    Launch Tower Setup
    Launch Tower Setup
 1. Tighten the ratchet straps while someone is holding a level tower, until the rail itself is vertical.
    Launch Tower Setup
    Launch Tower Setup
    Launch Tower Setup
 1. Make sure the ratchets are in the locked position after adjusting, all the way closed.
    Launch Tower Setup
   1. To unlock the ratchet strap, rotate the handle all the way back to the 180 degree position.
      Launch Tower Setup
 1. Hammer a steak into the small hole in the base plate of the tower.
 1. Adjust the angle of the antenna and tie off the antenna adjustment string to the cleats.
    Launch Tower Setup
    Launch Tower Setup
    Launch Tower Setup
 1. Install the umbilical, pinning one end of the umbilical to the tower clamp.
    Launch Tower Setup
    Launch Tower Setup
    Launch Tower Setup
 1. Hang the tower computer on the hook thats on the back side of the tower.
    Launch Tower Setup

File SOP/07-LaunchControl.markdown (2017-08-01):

---
title: Launch Control Setup
layout: base
---

# Launch Control Setup

## Equipment List

 - Two (2) Popup Tents
 - 2.4 GHz Helical and +12 Staff of Wifi
 - 2 meter J-pole and Mounting Bar
 - Base Tripod for J-pole and +12 Staff of Wifi
 - 2.4 GHz and VHF Feedline
 - TNC male to N male pigtail cable
 - Two (2) N female barrel 
 - N to reverse polarity TNC adapter
 - Launch Control Table (with inverter and VHF base station)
 - Radio Microphone
 - Extra Tables
 - Power Connector for VHF Base
 - Power Pole Connectors and Splitters
 - Batteries
 - Battery charger
 - Launch Control AP and Backup AP
 - Ethernet Cables
 - Power Strip
 - POE Injector
 - Trackmaster 3000
 - Telemetry Server

## Launch Control Setup

 1. Foldout legs of tables, setup popup tents
 1. Run power from generator to power strip
 1. Breakout power to battery charger
 1. Hookup batteries to charger and inverter
 1. Stand up and assemble the radio tower
 1. Run feed lines to attennas and stations
    - VHF base station
    - Launch Control AP
 1. Poweron everything
    - Inverter
    - VHF Base station
    - Launch Control AP

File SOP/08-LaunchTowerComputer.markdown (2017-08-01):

---
title: Launch Tower Computer (LTC) Setup And Configuration
layout: base
---

#  Launch Tower Computer Setup

## Procedures for LAUNCH TOWER

**Equipment List**

 - Launch tower computer
 - 2x 12 volt batteries with Anderson PowerPole (APP) connectors
 - Solar Panel
 - LTC Field Box
    - Ignitor cables
    - APP cables
    - Shorting bar (sometimes called "launch key", but really called "shorting bar")
    - N connector coax for LTC antenna

**Required Tools**

 - Miniature flathead screwdriver
 - Large Phillips screwdriver
 - DMM

### Mount To Tower

 1. **Mount** LTC box to the launch tower.
 1. Turn power and arming switches on side bulkhead to **off**.
    - Verify that the arming switch actually turns off using the DMM in "beep" mode
 1. Verify shorting bar is in place on side bulkhead.
    - Verify that shorting bar actually shorts using the DMM in "beep" mode.
 1. Check fuse on side bulkhead.

### Power Connections

Bottom Bulkhead

 1. Run **battery cables** though bottom bulkhead opening A, and connect to upper left Powerpole connector.
 1. Run **solar panel cables** through bottom bulkhead opening A, and connect to lower left Powerpole connector.
 1. Run **ignition cables** through bottom bulkhead opening A, and connect to upper right Powerpole connector.
    - Verify that the Away Box is empty (there's no shorting bar in it).
 1. Attach launch tower computer interlock box to LTC with caribiner
 1. Verify that the following indicators are illuminated:
    - **BATT** LED on the power interface board
    - **SOLAR** LED on the power interface board

### Data Connections

1. Connect rocket umbilical cable to connector on lower left of bottom bulkhead.
1. Connect WiFi antenna cable to connector on lower right of bottom bulkhead.

### Power-On

Side Bulkhead
BeagleBoard

 1. Launch control prepares for LTC bring up. Coordinate with launch control to proceed
 1. Turn on the red LTC power switch on side bulkhead. (It should illuminate)
 1. Verify that the following indicators are illuminated:
    - LTC power switch
    - **PWR** LED on power interface board
    - **5V** LED on power interface board
    - **PWR** LED on ignition board
    - **Power** LED on BeagleBoard
    - **USB** hub power LED on BeagleBoard
 1. _Notify launch control team that LTC has been powered on_.  Wait for launch control team to confirm a remote connection to the LTC.
 1. Replace bottom bulkhead cover plate.
 1. Connect internal **ignition battery**. _Notify launch control team_. Wait for confirmation.

Launch Tower done, unless a launch test is requested.

## Procedures for LAUNCH CONTROL

 1. Make sure Launch Control is set up
 1. _Wait for notification of LTC poweron_
 1. Begin to ping the LTC on the wireless address
 1. Start launch tower computer software:

         $ ./ltc.py

 1. Wait for launch-tower-comm to connect
 1. If launch-tower-comm does not connect, you may need to start the phidgetswebservice (it is automatically executed on system boot). To do this:
    - Open ssh session on LTC. Login as `root` and execute:
 
            # phidgetwebservice21 -v

## LTC Poweroff Sequence

 1. Confirm filesystem is in read-only mode
 1. `# poweroff -t now`
 1. Turn off power switch.

## Reference

### Suggested Radio Responses

1. LTC is connected to network: "I see your beagles coming in hot." -- Nathan
1. Confirm LTC you heard LTC is up: "Copy. Hot dogs on the move." -- Theo

Hot Beagle

### LTC User Accounts

 Username | Password
 -------- | --------
 root     | psaslv1b
 ltc      | ltc

### LTC Network Configuration

 Parameter                  | Value
 -------------------------- | -----
 WiFi (wlan0) IP Address    | 10.0.0.2
 Ethernet (eth0) IP Address | 10.10.10.1
 USB Wifi Mac Address       | 00:c0:ca:32:b7:17
 Ethernet Mac Address       | 2a:d3:77:aa:1e:f7

### LTC WiFi Access Point Configuration

 Parameter        | Value
 ---------------- | -----
 Channel          | 802.11b ch. 11
 SSID             | psas
 WPA-2 Passphrase | psasrocket
 AP IP Address    | 10.0.0.0/24
 Static Range     | 10.0.0.1 - 10.0.0.9
 DHCP Range       | 10.0.0.10 - 10.0.0.249

### Common LTC Commands

 - Reboot computer without delay:

        # reboot –t now

 -  Shut down computer without delay:

        # poweroff –t now

 - View IP addresses assigned to network interfaces:

        # ip address show

 - Make filesystem read/write

        # remount_root_rw

 - Make filesystem read only

        # remount_root_ro

### Figures

Bottom Bulkhead

Power Interface Board

Ignition Board

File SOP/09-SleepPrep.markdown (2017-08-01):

---
title: Sleep Prep
layout: base
---

# Sleep Prep

 - Charge Opal Data Logger
 - Charge TeleMetrum
 - Turn Off LTC
 - Bring batteries inside for temperature stability

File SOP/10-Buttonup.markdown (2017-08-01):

---
title: Rocket Button Up
layout: base
---

# Final Rocket Button Up

## ARTS-2

### Program the ARTS-2

 1. Connect 9v power, and RS-232 serial cable
 1. Start up Data Analyzer application from Ozark Aerospace
 1. Specify com port if necessary

### Verify correct operation of ARTS-2

 1. Goto altimeter -> diagnostics
 1. Press chirp to test tone generation
 1. With pyros disconnected, click boomer/sw, both pyros should show bad. Switch 2 should show 'off', and switch 1 show 'on'
 1. Connect the resistor/led combo to each pyro channel, click boomer/sw to verify that the respective channel shows OK. Also test-fire each pyro with the respective LED to make sure it lights the LED.

### Setup profiles

 1. We will be using flight profile 1 (one). Make sure respective dip switch on (dip switch 1 should be 'On')
 1. Goto the Altimeter -> Configuration
 1. Verify Profile 1 is configured to deploy drogue at apogee, and main at 1000ft, with a 50hz sample rate. You can 'Load from Alt', and verify these numbers, and 'Save to Alt'. When saving to alt for profile 1, you'll hear 1 beep.
 1. Verify Profile 2 is configured do deploy channel 1 at apogee, channel 2 at 1000ft, and a 50 hz rate... Just to be safe, save this to the altimeter. When saving to alt for profile 2, you'll hear 2 beeps.

## Avionics Module

### Firmware
 1. Begin with the Avionics stack outside of the CPA airframe section.
 1. Build the following stm32 projects in flight configuration (in the individual project directory `make flight`). Your repo should not have any uncommited changes.
   - flight-gps
   - flight-imu
   - flight-rnh
   - flight-servo
 1. Connect JTAG debugger to each of the physical microcontroller boards in turn and flash the correct firmware to it using `make write_stl`.
 1. Using Commander turn on each of the boards.
 1. Use telnet to verify that the boards are talking and return the correct version string.
    - All versions should have the flight- prefix, have the same 7 character hash, and not have M appended to the end.

## Payload Module

### Pre-Assembly

 1. Check Battery voltages
    - ARTS
    - TeleMetrum

### Assembly

 1. Cabling:
    - PWM cable to roll control servo
    - RNH To RasPiCam in payload bay
    - Screw in connectos
    - RasPiCam to 360 camera connector
    - Pyro (to recovery) must go up channels to not interfere with camera module
 1. Check 9 V leads are terminated into ARTS
 1. Aeroshell:
    1. Slide aeroshell down so the square hole lines up with the APS in the front of the camera sled
    1. Slide until flush with top of module
 1. Camera block
    1. Double check SD card is in place and tapped in.
    1. Screw in camera block
 1. Recovery:
    1. Leave off until 11-PreLaunch
 1. Motor Module:
    1. Attach spincan/motor mount but leave motor out until 11-PreLaunch
# Post Assembly tests
 1. Verify Rocketready works using the dev umbilical cable

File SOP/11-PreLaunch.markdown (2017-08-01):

---
title: Pre Launch
layout: base
---

# Pre Launch

## Launch Control Setup

### Radio Checks

 1. 2 meter mobile on and locked on PSAS freq (see References)
 1. Sound-off personnel with HTs
 1. PSAS Linksys router up and running
 1. Setup Telemetry server
 1. Plug in TM3K
    - ping to verify

## Procedures for LAUNCH TOWER

#### Tools for On Tower Procedures

 - Procedure book
 - Small flashlight to view inside aeroshell
 - Medium flat-head screw driver, for main switches, make sure it will fit thru the aeroshell holes
 - Flight Umbilical cable
 - Motor box
   - Igniters
   - Dowel for igniter

#### LTC On
 1. Verify Igniters **NOT in**
 1. Power on LTC
 1. _Call launch control for LTC update_
 1. Attach umbilical cable
 1. _Call launch control for FC update_
 1. Test umbilical connector disconnector disconnects correctly by physically lifting the rocket on the launch rail.
 1. _Call launch control to verify that they saw umbilical disconnect_
 1. Reattach Umbilical

## Procudures for LAUNCH CONTROL

### LTC On

 1. Wait for call from tower that LTC is on
 1. Verify LTC (ping)
 1. Bring up
    - LTComm
    - Commander
    - Telemetry window
       - Check for connected in top right
 1. _Call tower to continue and attach umbilcal_
 1. _Wait for tower to confirm conduct umbilical connector disconnector test via radio_
 1. When Away team has completed umbilical connector disconnector test, verify using telemetry that the umbilical has disconnected
 1. _Call tower to confirm we see detached umbilical_
 1. Check for umbilical reattachment. 
 1. Using Commander check umbilical by sending RNH version request
 1. Using LTComm, turn on shore power
    - Look for shorepower voltage within nominal bounds in LTComm
 1. Using Commander RNH tab, **Turn on FC**
 1. Wait for FC to boot (about 30 seconds)
 1. Verify Trackmaster power amp is on
 1. Turn on rocket wifi power amp
 1. Check telemetry server for FC packets

At this point we are set up physicaly. The tower crew can come back to launch control if they need water or there is an expected wait time for launch.

## Pre Launch Software Testing

### Power up

 1. Turn on all ports on the RNH using Commander
 1. Send version request and self test for each device using Commander
    1. RNH
        -  Verify port faults for no unexpected errors
    1. FC
    1. IMU
    1. Roll
    1. RasPiCam 1
    1. RasPiCam 2
    1. GPS

### Working Checks

 1. RNH
    1. Check telemetry viewer that port current draw is nominal
    1. Verify that umbilical detect is detecting the umbilical
    1. Verify battery is within nominal bounds and has no unexpected errors
 1. IMU
    1. In telemetry viewer look for data
 1. RasPiCam 1
    1. Bring up streaming view and check stream
 1. RasPiCam 2
    1. Bring up streaming view and check stream
 1. Roll
    1. Use commander to send Roll test command
    1. Watch fin movement through RasPiCam stream
 1. GPS
    1. In telemetry viewer wait for good GPS Lock
 1. Full system check:
    1. With IMU on, rotate the rocket about all axises for the IMU calibration procedure 

## Post Check Power Down

 1. SSH into the flight computer
 1. Manually stop the FCF service
 1. Purge the log files
 1. Set any and all flags to FLIGHT
 1. Shutdown FC
 1. Power off everything but RNH
    1. Use Commander to send **All Off** command
 1. Check that shore power is still on in LTComm
 1. Purge Telemetry logs and restart the telemetry server
 1. Attach recovery and motor modules
Now ready to continue to final launch countdown as window conditions allow.

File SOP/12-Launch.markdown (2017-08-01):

---
title: Launch Procedures
layout: base
---

# LAUNCH

## Procedures for LAUNCH CONTROL

### Trackmaster

 1. Plug in ethernet and power-over-ethernet (POE) injector.  

### Telemetry Server

 1. Boot telemetry server (laptop)

## Full Powerup

 1. With Rocket on pad and preped (see: Pre-Launch)
 1. Use commander to power all on
 1. Clear FC log files
 1. Attempt to verify telemetry
 1. Use commander to turn on the following
    - IMU
    - GPS
    - Raspberry Pi camera ONE
    - Raspberry Pi camera TWO
    - Roll
    - WiFi
 1. Verify data streams through telemetry server over trackmaster WiFi link
 1. Send version commands to:
    - IMU
    - GPS
    - Raspberry Pi camera ONE
    - Raspberry Pi camera TWO
    - Roll
    - Flight computer
    - Rocket net hub

## Arm FCF

 1. Disable Shore Power
 1. Send ARM Commands

Proceded to Terminal Count

## Procedures for LAUNCH TOWER

## Final Pre-Launch Procedures

### Arm Recovery System

Payload module switch layout

1. Turn on TeleMetrum (SW 4)
    1. Listen for beeps. 3 beeps good, low tone bad, 10 seconds Morse P ( .--. )
    1. Radio down to launch control to verify telemetry is streaming.
    1. Radio down to launch control to verify configuration coming from TeleMetrum is as expected.
1. Turn on ARTs (SW 3), verify good beep code (3 beeps).

## Run Igniter Cables

 1. Lay out Ignition Extension Cable with 3 boxes.
    - Motor Box ~7ft away from nozzle.
    - Away Box as far as possible, but try to keep orange cord from being run over.
 1. _Call with Launch Control for go-ahead to hook up igniter_
 1. Clear all personnel other than L3
 1. Check Manual Arm switch on LTC is off.
 1. Check that the LTC igniter relay is off.
 1. Check that the RocketReadyRelay is off.
 1. Verify short bar/launch key is in place
 1. Check that the Away Box is empty (no shorting bar) and the light is off.
 1. Check that the LTC igniter relay and the RocketReadyRelay are off.
 1. Verify alligator clips are connected to the motor box.
 1. Insert motor igniter into motor.
 1. _Call Launch Control that igniter is in_ and confirm they understand..
 1. Verify Motor Box indicator is dark
 1. Connect the alligator clips to Igniter.
 1. Switch Manual Arm Switch to **ON**
 1. _Call Launch Control that Arm Switch is on_. Verify LC understands.
 1. Remove short bar/launch key.
 1. Move Away from the box.
 1. Final check that area is clear of other personnel.
 1. Verify that red LED in away box is OFF.
 1. Insert shorting jumper into the Away box
 1. Leave the Launch area (**run away**).
 1. _Call Launch Control that arming is complete_. Verify LC understands.

## Terminal Count

 1. Clear area for launch
    - All observers should look and affirm that no one is close enough to the tower that it's a problem.
 1. Check ground
    - Telemetry
    - Video
    - TeleMetrium
 1. Check GPS lock
 1. Get in positions
    - Recovery eyes up
    - Cameras set
    - Trackmaster and spotter
 1. Go/No-go poll
    - LTC (launch tower comm app)
    - Recovery (radio leads)
    - TeleMetrum
    - Video
    - Trackmaster
    - Telemetry
    - FCF
    - FD
    - RSO
 1. Turn on siren and light.
 1. Start countdown (30 seconds)
 1. Send ignite signal (T-0)

## Ignition Instructions

 1. Make sure the launch tower computer is operational and on the network
 1. From a computer on the ground network, run the kivy app with ./ltc.py found in the [launch-tower-comm/launch-tower-comm](https://github.com/psas/launch-tower-comm/tree/master/launch-tower-comm)
 1. The app will come up breifly in the disconnected state, and then establish a connection to the LTC. This is indicated by the status indicator in the top right displaying "Nominal". 
 1. Verify all the values in the sensor display widget (bottom half of screen) are nominal.
 1. To arm the launch tower shorepower must be off. Once it is so the tower can be armed by clicking the "Arm" button.
 1. In the Armed state the top left buttons will swap over to "Ignite" and "Abort", and the status indicator will indicate "Armed" in a red font.
 1. To return to the unarmed state click abort.
 1. To proceed with ignition, click the Ignite button. A popup will ask you to confirm this action.
 1. To command the igniter to ignite, click the ignite button on the popup. Otherwise you can click abort to return to Armed screen.
 1. Once the popup ignite button has been pressed it will return to the Armed screen. When the LTC has confirmed that the igniter is active the Ignite button will turn blue and the status indicator will show "Ignited!" in teal text.
 1. Verify the rocket has launched. Visual cues include the rocket no longer being on the launch tower and a smoke trail leading off into the sky. Auditory cues include loud noises. 
 1. The LTCcom software will automatically turn off the igniter after 10 seconds. By pressing either the Ignite or Abort buttons the command to shut off the igniter can be sent early.

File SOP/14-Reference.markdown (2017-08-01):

---
title: Reference
layout: base
---

# Reference

## Radios

Standard comm frequencies:

 - 2-meter: **146.430 MHz**

### Area Repeaters

 - Pine Mountain W7JVO: `146.700-` tone: `162.2`
 - Pine Mountain W7JVO: `444.750+` tone: `156.7`
 - Mt Hood: `147.120+ 100hz`
 - Mt Hood: `147.120+ 100hz`
 - Bend - Awbrey Butte `147.040+ 100.0 hz`

### Call Signs

 - `KD7CJT` Andrew
 - `KF7RAS` Nathan
 - `KJ7SU`  Glenn
 - `KF7CZB` Dave C.
 - `KC7KWX` Casey
 - `KF7VJX` Jenner
 - `KE7EKT` Jamey
 - `KE7EKR` Sarah
 - `KD7SQG` Keith P.
 - `KD7SQH` Bart
 - `KF7NLF` Kenny
 - `KG7DBF` Gavin
 - `KG7EYD` K

## Frequncies

Frequency Allocation

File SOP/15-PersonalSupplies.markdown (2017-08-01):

---
title: Personal Supplies
layout: base
---

# Personal Supplies

The purpose of this list is to give ideas to attendees as to what they should bring.
It can freeze at night and can be over 100 deg. F during the day.
This trip: should not freeze at night, expect 90s during the day Sunday.

## Life Functions per person

These things should be on hand per person.

 - Water: lots of water, there is none on site
 - Food: dinner, breakfast, lunch, dinner and snacks
 - Coffee or tea or energy drinks
 - Any pharmaceuticals or medial supplies you need to sustain life **and** methods for storing them in the desert heat/cold

## Keep you cozy

 - Flashlight
 - Sunscreen
 - Camelback or way to carry water without holding
 - Canteen or water bottle
 - Dishes to eat off of and with
 - Way to cook your food
 - Sleeping bag
 - Toothbrush
 - Deodorant
 - Pillow
 - Teddy Bear :)
 - Tent or cover
 - Change of clothes: Cold at night, usually hot during the day
 - Sun Glasses
 - Sandals
 - Shoes
 - PSAS shirt
 - Chair
 - Towel
 - Toilet Paper (Just in case)
 - Hat that covers the neck

## Extras

This list will be more random, but worth listing as most pertain to more than one person.

 - Tripoli card
 - Ham radios
 - Family band radios
 - Radio antennas, hand mics, way to attach to body
 - Extra batteries
 - Laptop
 - Tripod
 - Camera and lenses
 - Memory cards, usb sticks
 - DC and AC chargers for various equip. (phone, radio, laptop, gps, flashlight)
 - Music and headphones
 - Note taking things: Paper portable, electronic
 - GPS
 - USB to Serial adapter
 - Serial to TTL or USB to TTL
 - Video camera
 - Binoculars
 - Sun shade / open walled tent / canopy
 - Clock or watch for ground station
 
## Tools

General list, name by what you are bringing if you would like to get a count.

 - CA (Cyanoacrylate)
 - Gorilla Tape
 - Butane soldering iron

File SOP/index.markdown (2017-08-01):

---
layout: base
title: PSAS Procedure Book
---

# Procedures:

 1. [Development](01-Development.html)
 1. [RocketTable](02-RocketTable.html)
 1. [FlightDirectorTable](03-FlightDirectorTable.html)
 1. [DropTest](04-DropTest.html)
 1. [Flight](05-Flight.html)
 1. [LaunchTower](06-LaunchTower.html)
 1. [LaunchControl](07-LaunchControl.html)
 1. [LaunchTowerComputer](08-LaunchTowerComputer.html)
 1. [SleepPrep](09-SleepPrep.html)
 1. [Buttonup](10-Buttonup.html)
 1. [PreLaunch](11-PreLaunch.html)
 1. [Launch](12-Launch.html)
 1. [Contingency](13-Contingency.html)
 1. [Reference](14-Reference.html)
 1. [PersonalSupplies](15-PersonalSupplies.html)
 1. [Inventory](16-Inventory.html)

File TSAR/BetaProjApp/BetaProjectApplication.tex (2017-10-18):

%Preamble
\documentclass{article}
%packages
\usepackage[utf8]{inputenc} %Unicode support
%\usepackage{ngerman}{babel} %Change hyphenation rules
\usepackage{hyperref} %add links to your document
\usepackage{graphicx} %add pictures to document
\usepackage{listings} %source code formatting and highlighting
%\usepackage{tikz}
%\usetikzlibrary{shapes,arrows}
\begin{document}
\author{Mark Musil Junior Elec. Eng. (Point of contact) - mmusil@pdx.edu}
\title{TSAR Beta Application}
\date{October 13, 2017}
\maketitle{}
Additional team members:
Chuck Faber Freshman Elec. Eng. (other team members being recruited presently)
\section{Objective}
The TSAR group will build an embedded controls and data acquisition system (CDAQ) for a liquid fuel rocket engine test stand for the Portland State Aerospace Society. Solving this issue is vital because developing a liquid fuel rocket engine will decrease PSAS’s cost per launch drastically while also opening the door for considerably higher peak apogees. Without the development of a safe CDAQ solution for the test stand, PSAS cannot reach its goals. The TSAR solution is a student led, in house solution which will create a custom taylored, safety oriented soluton for test stand CDAQ. Our solution is unique because it will be entirely open-sourced with a focus on repeatability and simplicity to allow other amateur rocket groups to benefit from the liquid rocket engine technology. We will use an off-the-shelf Beagle Bone Black embedded computer and a Marionette DAQ board (a former PSU capstone) to implement this system and all software will be developed by the TSAR team of PSU undergraduates.
\section{State-of-the-art}
Data acquisition systems exist for rocket engine testing such as NASA’s NDAS system but are prohibitively expensive and are geared toward orbital launch vehicles, hardly meeting PSAS’s needs. TSAR provides a framework for any amateur aerospace enthusiast to design a liquid fuel engine test stand, with the cost of materials being realistic for even an individual. Furthermore, our group is building in house force sensors to solve the problem of cryogenic flow monitoring. We will be pioneering these sensors and documenting them publicly on GitHub, thereby providing one more tool for the amateur aerospace community. Finally, we will be creating a custom SCADA (Supervisory Control And Data Acquisition) style interface which will allow real time data monitoring from any laptop computer. 
\section{Future Output of the Project}
By the end of this project, we will have created a working prototype of hardware and software that will automatically conduct the entire firing sequences with little to no user-input required during the sequence. The system will concurrently record data, respond to changes in the system, and enact constant hazard checks and procedures to ensure safe use of the test stand.

Our final product will not only be the working CDAQ, but a GitHub repository of well documented, thorough guides to designing each and every aspect of the completed system. Our solution is innovative because of this open-source aspect. Athough DAQ systems exist, they do not exist as community based resources for other amateur rocket groups.
\section{Work Plan and Milestones}

\textbf{October 2017}: First team meeting Friday October 20. Complete thorough system block diagram. Consult with Doug Hall about best programming language/approach to the controls problem. 
\textbf{November}: Begin testing Beagle Bone Black and Marionette Board. Attempt a board to board interface. Confirm actuators and sensors are to spec. 
\textbf{December}: Develop source code and begin interfacing with actuators and sensors. 
\textbf{January 2018}: Test system-on-board and begin integration with test stand. 
\textbf{February}: Functional testing
\textbf{March}: Submit completed system by end of spring break.
\section{Budget/Resources Needs} 
The current budget can be found on our
\href{https://docs.google.com/spreadsheets/d/1loLofdCxh_BdQxyFeZhvYgwQ_FHBo9597Mpg26gE-Iw/edit?usp=sharing}{Spreadsheet}.

https://docs.google.com/spreadsheets/d/1loLofdCxh_BdQxyFeZhvYgwQ_FHBo9597Mpg26gE-Iw/edit?usp=sharing

Budget not final and no purchases should be made yet if this project is selected for funding.
\end{document}

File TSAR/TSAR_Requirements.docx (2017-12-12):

Preamble

The Liquid Fuel Engine Test Stand (LFETS) Dashboard will be SCADA-like system for displaying the state of various actuators and sensors on the LFETS to provide user interface and manual control of the hardware. It will trigger and/or safe the system that automatically controls the ignition sequencing of the LFE. The system is required in order to prep, test, and fire the various hardware required for a LFE test and eventually a rocket launch.

Technical Requirements

1. The Dashboard must be usable without an internet connection, ie in the middle of the Oregon desert.
2. The project must be maintainable by students and future PSAS members. To this end, Python is the recommended language.
3. The interface must be graphical. PyQT has been recommended.
4. The software must receive data from, and send control signals to, a Marionette DAQ (http://marionette-daq.github.io/)-based system.
  a. Future: the Marionette may be directly attached to a Raspberry Pi, in which case the Dashboard will receive data and send commands over a LAN.
5. The system must be ‘easy to understand’, so that anomalies are immediately visible, without interfering with user operations (ie no modal popups)
6. The system should be scriptable, for closed-loop operations
7. The system should include events and triggers, for closed-loop operations
8. The system model shall be data-driven for maintainability.
9. The system should be able to dynamically generate network maps. NetworkX is recommended. https://networkx.github.io/

Functional Requirements

1. The interface shall graphically display the EGSE system model components.
2. The interface shall display floating-point information received from sensors.
3. The interface shall display discrete state information for sensors attached to actuators, etc.
4. The interface may have the flexibility to display external inputs (ie EGSE state estimation data) for the related components.
5. The interface may display non-EGSE information pertaining to launch operations, such as temperature, time, and wind data.
6. The interface shall respond to mouse clicks on ‘interactable’ objects by sending state change commands.
7. The dashboard shall respect ‘command lockout’ times, once a command is sent, with the exception of emergency overrides.
8. The dashboard may include a global command lockout, limiting the interface to display-only.
9. The dashboard may expect a certain response from commanded devices, such as an acknowledgement, or a report of a state change, within a given time frame.
  a. Failure to detect a state change will result in displaying an anomalous state
10. User actions shall be logged.
11. Anomalies shall be logged.
  a. Anomalies include out-of-range data, data loss, “bad inputs” (unexpected states)
12. Time series data from sensors may be aligned and logged.

Components

Device

A Device represents a physical object that may be composed of zero or more Sensors, zero or one Actuator, and a Dashboard Element.

A Device may be in one of many discrete states, including (but not limited to) ‘nominal’, ‘warning’, ‘error’, ‘disabled’, ‘valve-open’, ‘valve-closed’, and ‘changing state’. (Is the device state the responsibility of the device itself? It’s definitely based on the inputs upon the Device, ie sensors and actuator feedback)

PhysicalLinkage

A visually defined connection between two devices. Currently meant for visual reasons only, to better match the Dashboard interface with the

DashboardElement

Catch-all superclass for the View container that encompasses both the high-level information for a Device, the text and iconographic metadata for the Device, and the state of the Device.

Sensor

A component of a Device that links to a physical device via serial port or logical socket, and provides either a discrete state input, or a floating point input. A Sensor has a unit, a typical range, a warning state description, and an error state description.

The Sensor will also have a ‘data loss’ configuration, and will be contain the information required to detect if a Sensor’s input signal has not been received in a given period of time.

SensorStateDescription

A combination of a range and a time duration for a sensor to change states. For example, a temperature probe may report an error if the temperature is greater than 105 degF for more than 0.1 seconds or for more than 3 samples.

SensorTrigger

A SensorTrigger is a combination of a Sensor, a StateDescription, and a snippet of Python code that will execute if a specified sensor enters the specified state.

SensorLog

A logical class for capturing data, primarily time-series data. It shall record data with its accurate timestamp, and shall be used to perform network analysis after the test stand is used (if desired). The SensorLog may be accessed by other objects, to provide time-aggregate measurements on the dashboard (rolling avg, min/max, etc)

Actuator

A component of a Device that may be controlled by the Dashboard user, or by Dashboard scripts.

Task Priorities

The project’s rough order is as follows:

1. Build model describing the Devices, the connected Actuators and Sensors, and any physical linkages between the Devices.

Definitions

Interface is specifically the user interface, or the combination of the view and the controller.

Dashboard is the system as a whole, but may be seen as the Controller and the Model pattern.

System Model - the logical devices attached to the EGSE and connections between them.

EGSE - Electrical Ground Support Equipment

SCADA - Supervisory Control and Data Acquisition. SCADA generally refers to an industrial computer system that monitors and controls a process. In the case of the transmission and distribution elements of electrical utilities, SCADA will monitor substations, transformers and other electrical assets.

Time Alignment - the process of taking multiple inputs that arrive at different times, and recording the known value at a specified time interval. This should not be confused with a reading of the sensor, but is instead a reading of the dashboard.

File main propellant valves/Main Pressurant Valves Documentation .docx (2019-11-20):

# Main Fuel and Oxidizer Valve Actuator Design

## Revision History

Date | Version | Name | Update Notes
6/18/19 | 1.0 | Petr Mazhinikov | Initial writing
11/19/19 | 2.0 | Marc Wasserman | Major overhaul, added content from 2018 capstone reports, removed double spaces after periods (argh!)

## Background

The last valves before propellant reaches the engine are the main fuel valve and the main oxidizer valve. These valves are responsible for the control of the pressurized propellants to the engine. The main fuel valve will be located on the fuel side of the test stand and carry isopropyl alcohol. The main oxidizer valve will be located on the oxidizer side of the test stand which carries liquid oxygen. This document contains information on the valve actuators, which are required to attach to a manual ball valve and actuate the valve at pressures of >500psi. Additionally, the liquid oxygen valve will need a system to prevent frost both inside and outside of the valve. Finally, the actuator must be controlled remotely and provide absolute position sensing.

## Actuator Design

Current design files can be found in the Liquid Engine Test Stand (https://github.com/psas/liquid-engine-test-stand/tree/master/main%20propellant%20valves/MFV%20%26%20LOX%20Actuator) GitHub repo.


Figure 1: Main Fuel Valve Figure 2: Main Oxidizer Valve

The configuration of the actuator went through many iterations and ended with a 90-degree bevel gear design shown in Figure 1 and 2. Both designs for the LOX and fuel valve actuators are very similar in nature. The only difference between them are the valves themselves and the types of brackets used to connect the actuators to the valves. To crack open and close the valves, a 12V 23 rpm DC motor is used, which will open the valve to open in about 1.25 seconds. The frame, motors, and supports are all parts specified from from servocity.com and are primarily standard Actobotics brand components. The brackets were made in-house using sheet metal and hand tools.

The purpose of placing the motor at a right angle is to provide access to the gear shaft to allow mounting of a the position sensor. The position sensor specified for the project is a magnetic hall-effect sensor that utilizes a special magnet which must be rotated near the sensor IC. The sensor is mounted via a second non-magnetic coupler placed on top of the gear shaft and the sensor board is mounted to the underside of the top plate. Two secondary advantages of the bevel gear is that is allows for the mounting of different motors without changing the gears and also provides a 2:1 reduction which doubles the torque.

## Position Sensing

The position sensing for the actuator will be accomplished using an AMS AS5047 magnetic position sensor. This sensor utilizes the Hall Effect to detect the rotation of a magnet placed near to the sensor IC as shown in the diagram below.

2.1 Mounting the AS5047P adapter board Figure 3: Mounting and dimensions o. 5-3mm 22mm 00000000 000010000 w/ 000 4x2.6mm

Figure X: AS5047 evaluation board with clearances and mounting shown, https://media.digikey.com/pdf/Data%20Sheets/Austriamicrosystems%20PDFs/AS5047P-TS_EK_AB.pdf

The sensor can be read over a standard serial interface and provides absolute position sensing with a 14-bit resolution. This type of sensor is common in industrial and automotive applications and is more robust than a potentiometer-based sensor as there is no contact between the magnet and sensor. Care must be taken, however, to ensure clearances are maintained and ferrous materials are placed far enough away from the sensor to avoid interference.

## Liquid Nitrogen Testing


Figure: bucket full of liquid nitrogen with a valve shoved in it

A test was conducted in spring 2019 to gather information on any torque changes that happen when exposed to cryogenic liquids, and if a greater torque motor was required. The test consisted of using liquid nitrogen, which is much safer to handle than liquid oxygen, to simulate cryogenic flow. The LOX valve was tested at room temperature and after being submerged for an extended time (no record of amount of time) in liquid nitrogen. A moment arm and force meter were used to determine actuation torque (no record of length of arm) and a thermocouple was used to measure valve temperature. Through varying time intervals of the valve being submerged the torque was found to vary as seen in Fig. 5 and Fig. 6.


Figure X: Valve at room temperature. First peak (2.35 ft lb) is the valve starting to open, followed by a second peak when the valve is fully open | Figure X: Valve at first exposure to cryogenic temperature. First peak (3.03 ft lb)

The valve requires an increase of 0.68 ft lbs in torque when it was first exposed to the cryogenic temperature shown in figure 6. The valve itself underwent a temperature change of -74.5 C and maintained an average temperature of - 93.2 C. After the initial exposure, the valve went back to the same torque range as the room temperature one shown in figure 5. From the data gathered it was concluded that using a motor with about 3.5 ft-lb (4.75 Nm) of torque is sufficient to open the valve under cryogenic temperatures. It is not known how torque requirements will change with pressure, however due to a miscommunication between teams, the motor and gear train was specified to provide 35 ft-lb of torque, so it may not matter.

## Valve Freeze Mitigation

In consultation with industry advisors, the team became aware that a challenge with the cryogenic valves in a rocket system is the tendency for moisture to condense out of the air and freeze either inside or outside of the valve body, causing the valve to freeze in place. Mitigation strategies for this will involve an inert gas purge of the lines and tanks before filling and an inert gas purge of the LOX valve continuously beginning when the liquid oxygen tank is filled.

At this time, the team plans to design a case for the liquid oxygen valve and actuator with ports to allow for a slow N2 purge to prevent moisture buildup, however this has not yet been designed or manufactured.

## Valve Actuator CAD

<need to insert drawings of the valve actuators>

Link to current CAD: https://github.com/psas/liquid-engine-test-stand/tree/master/main%20propellant%20valves

## Valve Actuator BOM

Link to current BOM: https://docs.google.com/spreadsheets/d/1h27afDgpPqDNQtMSQFRr19zuC3EtCLTjsB5sXuKFS4k/edit?usp=sharing

Main Fuel Valve Actuator
Part # | Manufacturer | Description
39036 | Sharpe | Main Fuel Valve
- | Custom | Custom Base, sheet metal
535110 | Servo City | Pillow block & bearing, 1/4" bore
555188 | Servo City | Motor mount
625112 | Servo City | Coupler, set screw, 1/4" to 5/16"
634070 | Servo City | D-shaft, 0.25x2.25 in
625100 | Servo City | Coupler, clamping 1/4"
535130 | Servo City | Bearing block, 1/4" bore
637222 | Servo City | Bevel Gear Set
585444 | Servo City | Standard channel, 4.50"
634068 | Servo City | D-shaft, 0.25x2.0in
AS5047Eval | Digikey | AS5047 Evaluation Board (magnetic sensor)
585422 | Servo City | Flat plate, 1.5x3in
? | Servo City | Standoff, 1/2in, 4 pack
? | Servo City | Standoff, 5/8in, 4 pack
632110 | TBD | 6-32 screws, length TBD, 25-pack (3/8"?)
| Pololu | G2 high current motor driver
638266 | Servo City | Heavy duty motor, 23rpm
LOX Valve Actuator | | (these parts are in addition to the parts above except as noted)
Part # | Manufacturer | Description
| Custom | Custom bracket
634074 | Servo City | d-shaft 0.25x2.5
634076 | Servo City | d-shaft 0.25x2.75
625114 | Servo City | shaft coupler 1/4" to 3/8"
625106 | Servo City | shaft coupler 1/4" to 6mm

## Initial Test Results

The main fuel valve actuator was initially assembled and some basic arduino code was written to test the functionality of the actuator. The motor specified had more than enough torque to operate the valve, however it was discovered upon testing that the commercial couplers attaching the gear shaft to the top of the valve stem was inadequate. The coupler allowed ~5 degrees of play in both directions, causing the valve to wander over multiple open/close operations. A custom coupler with a machined slot may need to be manufactured to reduce play. Additionally, to facilitate testing, the coupler that holds the position sensing magnet to the top of the gear shaft was 3d printed. A metal version will need to be manufactured for use in the actual hardware.

## Next Steps and Recommendations

1. Manufacture a custom coupler with tighter tolerances and retest actuator assembly
2. Manufacture a metal coupler to hold the position sensing magnet
3. Review and revise arduino test code to ensure:
  a. Bug-free operation
  b. Error handling
  c. I/O compatibility with the TSAR central controller
4. Design an external N2 purge system for the LOX valve assembly
5. Integrate valves and actuators into test stand and test operation under pressure

## Actuator Arduino Test Code

Please check github for code updates (https://github.com/psas/liquid-engine-test-stand/tree/master/main%20propellant%20valves/Arduino%20code%20for%20Testing/New%20Test%20Code/New_Test_Code), however sample code for initial valve operation testing is provided below for reference:

/*******Hydrotest code for Main Propellant Valves*********

7/30/19

Functions:

- Reads data from AS5047 rotary encoder over SPI interface

- Drives valve open 90 deg or closed 90 deg on button press via Pololu G2 motor driver

- Allows adjustments of position in 3 degree increments (or arbitrary)

- Note - program re-zeroes on startup, so reset arduino after making open/closed position adjustment

- Note - motor driver accepts PWM for speed control, however full speed is desired, so motor pin is driven HIGH or LOW.

SPI Fuctions

UNO: MOSI pin 11

MISO pin 12

CLK pin 13

CSN pin 10

*/

#include <SPI.h>

//Variables

int dir;

int actuate;

int set_angle;

int error_angle;

int zero_angle;

int delta;

int home_delta;

int buttonstate1;

int buttonstate2;

int buttonstate3;

int CSN = 10;

int SO = 12;

int SI = 11;

int CLK = 13 ;

unsigned int angle;

int pos;

//Definitions for motor output & button input pins

int pin_motor = 5;

int pin_motordir = 4;

int pin_button1 = 7;

int pin_button2 = 8;

int pin_button3 = 9;

void setup(){

//Set Pin Modes for magnetic encoder SPI interface

pinMode(CSN, OUTPUT);

pinMode(SI, OUTPUT);

pinMode(SO, INPUT);

pinMode(CLK, OUTPUT);

//Set Pin Modes for motor & buttons

pinMode(pin_motor, OUTPUT);

pinMode(pin_motordir, OUTPUT);

pinMode(pin_button1, INPUT_PULLUP);

pinMode(pin_button2, INPUT_PULLUP);

pinMode(pin_button3, INPUT_PULLUP);

//Set Slave Select High to Start i.e disable SPI chip

digitalWrite(CSN, HIGH);

//Initialize SPI

SPI.begin();

Serial.begin(9600);

SensorRead();

zero_angle = pos; //Read current position & save as zero_angle on startup.

Serial.println("Ready. Zero angle =");

Serial.println(zero_angle);

delay(500);

}

void loop() {

buttonstate1 = digitalRead(pin_button1);

buttonstate2 = digitalRead(pin_button2);

buttonstate3 = digitalRead(pin_button3);

if(buttonstate1 == LOW){

SensorRead();

home_delta = abs(zero_angle - pos); //Determine if currently in the home position

if(home_delta > 180) {

home_delta = abs(home_delta - 360);

}

Serial.println("degrees from home pos:");

Serial.println(home_delta);

if(home_delta < 10) { //Less than 10 degrees from home, drive to +90

set_angle = (zero_angle + 90);

set_angle %= 360;

dir = 0;

}

if(home_delta >= 10) { //More than 10 deg from home, drive to home position

set_angle = zero_angle;

dir = 1;

}

// set_angle = (pos + 90); //Old logic, removed due to possible accumulating errors

// set_angle %= 360;

Serial.println("set angle:");

Serial.println(set_angle);

DriveLogic();

}

// Experiment to see if you can budge the valve with a button press

if(buttonstate2 == LOW){

SensorRead();

set_angle = pos + 3;

set_angle %= 360;

Serial.println("Adjust +3 degrees");

dir = 0;

DriveLogic();

}

if(buttonstate3 == LOW){

SensorRead();

set_angle = pos - 3;

if(set_angle < 0){

set_angle += 360;

}

Serial.println("Adjust -3 degrees");

dir = 1;

DriveLogic();

}

/**********Test of functions:*************

MotorCommand(1);

delay(1000);

SensorRead();

Serial.println(pos);

MotorCommand(0);

delay(1000);

SensorRead();

Serial.println(pos);

*/

}

// ***************Auxiliary functions****************

void SensorRead() {

SPI.beginTransaction(SPISettings(10000000, MSBFIRST, SPI_MODE1));

//Send the Command Frame

digitalWrite(CSN, LOW);

delayMicroseconds(1);

SPI.transfer16(0x3FFF);

digitalWrite(CSN,HIGH);

//Read data frame

digitalWrite(CSN, LOW);

delayMicroseconds(1);

angle = SPI.transfer16(0xC000);

digitalWrite(CSN, HIGH);

SPI.endTransaction;

angle = (angle & (0x3FFF)); //This is a bitwise AND - not sure why it is here?

pos = ( (unsigned long) angle)*360UL/16384UL; //convert 14 bit to angle

}

// *****MOTORCOMMAND,(1)=ON,(0)=OFF*****

void MotorCommand(int actuate) {

if(actuate == 1) {

digitalWrite(pin_motordir,dir);

digitalWrite(pin_motor,HIGH);

}

else {

digitalWrite(pin_motor,LOW);

}

}

void DriveLogic() {

SensorRead();

delta = abs(set_angle - pos); //intermediate variable to determine min angle between

if(delta > 180) {

error_angle = abs(delta - 360);

}

else { error_angle = delta;

}

while(error_angle >= 3) { //Adding several degrees to allow for stopping time

SensorRead();

delta = abs(set_angle - pos); //intermediate variable for 360 degree rollover handling - needs optimization

if(delta > 180) {

error_angle = abs(delta - 360);

}

else { error_angle = delta;

}

// if(error_angle > 95){ //Dheck if error overrun exists & stop motor

// break;

// }

MotorCommand(1);

Serial.println("Motor on, error_angle =");

Serial.println(error_angle);

}

MotorCommand(0);

}

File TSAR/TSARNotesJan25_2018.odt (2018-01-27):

TSAR Team Meeting

26 January 2018

Attendees

Agenda

Last Meeting Follow up

1. We now have a mechanical calibration system for the pressure transducer calibration.


2. Decided on the power system – lift the ground


Figure 1: Automotive analogy for ‘lifting’ the ground of a circuit.

3. Ordered a few misc. Components for the LT1371 29V

New Info

1. Test stand meeting Thrusday at 4:30

2. Add a 1N4004 rectifier diode in parallel with the solenoid (relays, etc) and any inductive loads.

Member Updates

What did you do last week?What will you do this week? Are there any impediments in your way?

Action Items/Next Steps

    Mark – email peter and arman about power issues.

Anyone – work on:

1. Building Power supplies

2. Calibrating pressure transducers

3.

Next Meeting Agenda

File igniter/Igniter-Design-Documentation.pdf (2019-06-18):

Sam Hastings Hauss - samhauss@hotmail.com

## Igniter Documentation and Recommendations

Background Info

Liquid propellant rocket engines require a high energy ignition source. An inadequate source of ignition can lead a hard start, or the engine failing to ignite entirely. A hard start occurs when two combustion wavefronts exist in the combustion chamber due to pooling of the propellant mixture. In the best-case scenario, a hard start means rapid expulsion of gas from the engine resulting in a flameout. The worst-case scenario is catastrophic engine failure.

The common ways to ignite rocket engines are as follows:
- Pyrotechnic ignition – a glorified firework shoved up in thru the nozzle. An electric “match” lights it and then it lights the propellants coming out of the pintle. When the engine lights, it blows the whole thing out of the engine.
- Hypergolic ignition – Substances that spontaneously ignite when mixed together. This is a very reliable way to create ignition, but the substances used in this are very dangerous most of the time. Because of this, we decided not to pursue this route.
- Augmented Spark Torch Igniter – Uses a spark plug to combust fuel and oxygen in a small combustion chamber behind the rocket engine. This blows into the rocket engine through the back usually, like a torch

Augmented spark torch igniters are ideal in a lot of ways. For one thing, they are a reliable source of ignition, and if properly designed, are very repeatable (I.E won’t cause hard starts). Also, for engine testing, it means you can have multiple burns in a quick succession without having to manually “reset” the igniter.

A good source for info on augmented spark torch igniters: http://www.watzlavick.com/robert/rocket/

The engine that was designed for PSAS has a pilot hole in the back of it for an augmented spark torch igniter. This was the initial plan for igniting this engine, but as the 2.2kN engine is so small, it became clear that in order to mount the pintle with the correct pressure taps, it was going to be extremely difficult to fit the igniter. Furthermore, our capstone was on an extreme time crunch, and it would greatly simplify the test stand’s plumbing, and would be quicker/easier to design in general.

Discussing this with the engine capstone team, they said that the igniter hole in the back of the engine was put in place so that we would have the option of using an internal AST Igniter, but it was not required in order to light the engine. Because of this, we decided to go for an external ignition system (see fig. 1).


Fig. 1: New proposed igniter position

Using an external ignition system on the rocket has a lot of benefits. Besides the mention about not having enough room in the back, benefits include:
- Simulating the ignition of the engine in the rocket – For weight savings, the engine that will be used in the final rocket will almost certainly have an external ignition. By using an external ignition source for the tests, we can see how well an ignition system works before using it on the rocket itself.
- If “catastrophic engine failure” happens, the igniter will be out of the way of the engine (instead of bolted to the back of it). This means that it has a much better chance of surviving.
- It gives us options for the ignition (we can use pyrotechnic or AST).
- If we use a torch ignition system, the fuel and oxidizer no longer need to be at 450+ psi, as it no longer remains in the combustion chamber after ignition.
- It can be much less complex than an internal ignition.

The largest difficulty of having an external ignition is resetting the igniter for subsequent engine tests.

Igniter Arm Design

To hold the igniter that we decide to use in place, we designed a hinged arm that would mount to the frame of the test stand. A solid metal hinged arm could protect any fuel/oxygen hoses from potential flame, and it would be easy to reset the igniter to the correct location. Our design would be spring-loaded, so that if it fails, the arm’s natural position is away from the engine. It would be held in place by an electromagnet, which is strong enough to hold against the force of the unburnt fuel and oxidizer spraying against it, but weak enough so that when the engine ignites, the arm will swing out of harm’s way. A mockup of this arm is shown in fig. 2.


Figure 2: Cad Mockup of Igniter Arm. Electromagnet will be positioned on “forearm”.

A CAD mockup of this armature can be found in the LFETS git folder, under “igniter”.

We did some fluid momentum calculations to see how much force is applied to the arm prior to combustion. The results are shown below:


These calculations show that there will be about 7.16N or 1.61lbF on the arm prior to combustion. To provide a factor of safety of 2, we should design for about 3lbF pushing at the end of the 18” forearm.

The electromagnet that was purchased was advertised as a 55lb magnet but testing of the holding force of the magnet on the actual arm showed that the magnet let go at about 15-20lbF. This means the electromagnet should be placed at least 4” away from the fulcrum point to provide enough holding force for the arm.

The elbow joint of the arm has already been assembled in a way that minimizes play in the hinge joint. It resides in the LFETS cabinet of the rocket room. See Fig. 3:


Fig. 3: First Iteration of arm construction. Position on stand should be reversed 180 degrees, so that it will be directly outside of the engine.

Ignition Source

The igniter arm could be used with various ignition sources. The latest design iteration for an ignition source consists of a modified brazing torch placed on the end of the arm, used a bit like an augmented spark torch igniter. This design is subject to change based on the results of further tests (ex. hot flow pintle test).

The brazing torch will be grounded and an insulated wire will be brought out to the end of the nozzle of the torch. A model airplane ignition attached to a servo PWM generator will be used to generate a near-continuous spark at the tip of the torch to ignite it.

The fuel and oxygen supply will be mounted to the stand, regulated, and then attached through 2 solenoid “GEMS” valves. The fuel and oxygen lines will then be attached to flex line ran through the arm and out to the torch body.

Almost all of the parts have been acquired for this ignition system, apart from the material for the torch body or any experimental torch tips that we would like to try. However, it has not been assembled yet.

A concern of this design is that the torch flame may get “blown out” prior to ignition. Another concern is that the pintle may get overheated. Because of this, the design should be validated at first by itself, and then in a hot flow pintle test. This test consists of firing the pintle injector without the engine. A slow motion camera should be pointed at the pintle during this test so that the ignition flame front can be observed. The ignition of the propellant of this test should have a single flame front, and should consistently ignite the propellants in each test.

As a backup strategy, pyrotechnic ignition may be a good option, although this has not been explored as much. In a pinch, a decent pyrotechnic ignition option might be a road flare or sparkler with an electric match on it. Any pyrotechnic ignition could be easily adapted to fit the end of the arm.

Recommendations:

My recommendations regarding the igniter are dependant on a few things. First of all, I think there is value in completing the design of an internal spark torch igniter. The benefits of the predictable, repeatable ignition source make it worthwhile for future engine testing, and a well designed internal spark torch igniter can be used throughout multiple engine iterations.

With this being said, I would recommend that the design and construction of an internal spark torch igniter should be its own capstone project. Although the design of a spark torch igniter has already been started by Adam Harris, there is enough iterative design work and testing involved that it should keep a capstone team busy for a year, and if they finish early, they could explore pyrotechnic ignition as a backup strategy.

If PSAS decides to go this route, PSAS’ next iteration of engine should have more care taken for the interface of the igniter to the back of the engine. I believe it would be easier to design the igniter first, and then design the engine considering the position and mounting of the igniter.

However, if an engine is to be tested prior to an internal spark torch igniter capstone, the armature/external ignition system should be developed/used. Although this ignition system is much more crude, it is simpler and less time consuming to design, and a large portion has already been designed. As previously stated, the biggest issue with the external ignition arm design is the fact that it needs to be reset for each successive engine test. This is the largest design obstacle to overcome.

An option for resetting an external ignitor that I was thinking about is a winch system to pull the arm back into place.

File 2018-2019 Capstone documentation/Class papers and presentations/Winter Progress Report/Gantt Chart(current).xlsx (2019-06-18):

Liquid Propellent Engine Test Stand Integration and Testing ■ Completed ■ Elapsed ■ Remaining | 2019-01-06 | 2019-01-13 | 2019-01-20 | 2019-01-27 | 2019-02-03 | 2019-02-10 | 2019-02-17 | 2019-02-24 | 2019-03-03 | 2019-03-10 | 2019-03-17 | 2019-03-24 | 2019-03-31 | 2019-04-07 | 2019-04-14 | 2019-04-21 | 2019-04-28 | 2019-05-05 | 2019-05-12 | 2019-05-19 | 2019-05-26 | 2019-06-02 | 2019-06-09
Pintle Test
Water Test Pintle V1 | -1 | -1 | -1 | -1 | -1
Analysis of Pintle V1 Test |  |  | -1 | -1 | -1 | -1
Design Pintle V2 |  |  |  |  |  | -1 | -1 | -1 | -1 | -1 | -1
Manufacture Pintle V2 |  |  |  |  |  |  |  |  |  |  | 1 | 1 | 1
Water Test Pintle V2 |  |  |  |  |  |  |  |  |  |  |  |  | 1 | 0 | 0
TEST STAND
CAD
Pressure Section |  |  |  |  |  |  | -1 | -1 | -1 | -1 | -1
IPA Section |  |  |  |  |  |  | 1 | 1 | 1 | 1 | 1
LOX Section |  |  |  |  |  |  | 1 | 1 | 1 | 1 | 1
HARDWARE
Pressure Section Ordered |  |  |  |  |  |  |  |  | 1 | 1 | 1 | 1
IPA Section Ordered |  |  |  |  |  |  |  |  | 1 | 1 | 1 | 1
lox Section Ordered |  |  |  |  |  |  |  |  | -1 | -1 | -1 | -1
Pressure Section Installed |  |  |  |  |  |  |  |  |  | 1 | 1 | 1 | 1 | 0 | 0
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

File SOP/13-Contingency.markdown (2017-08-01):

---
title: Contingency
layout: base
---

# Contingency

## Ignition Failure

Recycle the launch

 1. **SAFE** Command to FCF
 1. Restart logging on 
    - Trackmaster
    - Telemetry server
 1. Get in positions
    - Recovery eyes up
    - Cameras set
    - Trackmaster and spotter
 1. Go/No-go poll
    - LTC
    - Recovery
    - TeleMetrium
    - Video
    - Trackmaster
    - Telemetry
    - FCF
    - FD
 1. **ARM** rocket
 1. Start countdown
 1. Send ignite signal

## Repeat Ignition Failure

 1. **SAFE** rocket FCF
 1. Turn on shore power
 1. Turn off WiFi
 1. Wait
 1. Approach tower
 1. Undo short bar an disarm LTC
 1. Determin root cause
 1. Restart from end of Pre-Launch

## Fire Near Rocket

 1. **SAFE** rocket FCF
 1. Inform LCO of situation
 1. Turn off shore power
 1. Send All Off to rocket
 1. Send water and shovel people
 1. Start over with On Tower Procedures

## Fire After Launch

 1. Keep core team focused on rocket
 1. After parachute is seen send water and shovel people

## CATO

 1. Double check personel (nearest people OK)
 1. Send fire and water people
 1. Bring down loggers
 1. Save logs to multiple disks
 1. Turn off LTC
 1. First people to site must take detailed photos of area before touching anyting

## Shred

 1. Double check personel (nearest people OK)
 1. Bring down loggers
 1. Save logs to multiple disks
 1. Start looking for parts
    - Take photos/GPS lat-lon of each piece as it is before touching or moving

## Drouge Doesn't Deploy

 1. Heads up
 1. Keep tracking
 1. Get shovels
 1. Copy off data to multiple disks

## Main doesn't deploy

 1. Send recovery team
 1. Get photos and lat-lon before touching

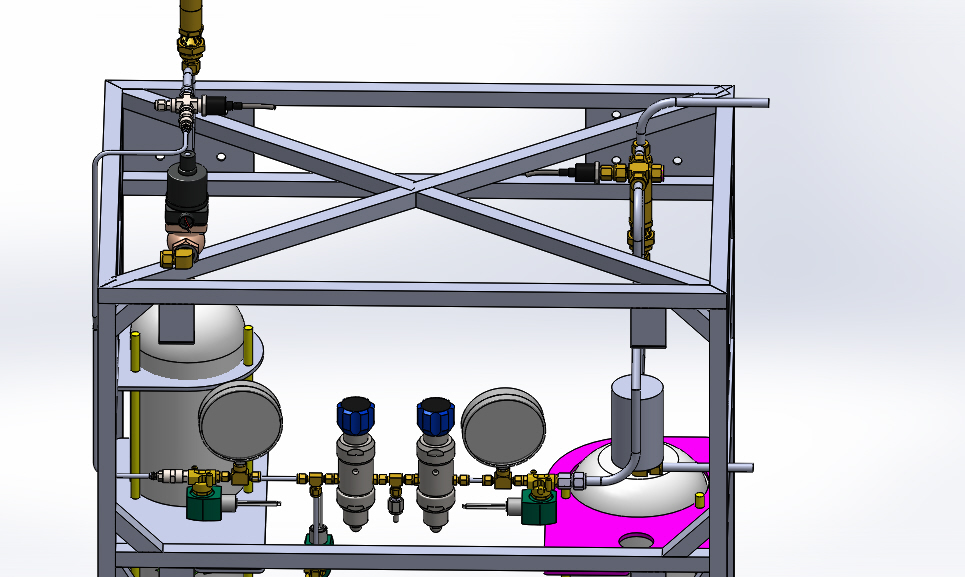
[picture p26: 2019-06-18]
2018-2019 Capstone documentation/Class papers and presentations/Images of Standy stuff/LMTS_5 upper section.JPG

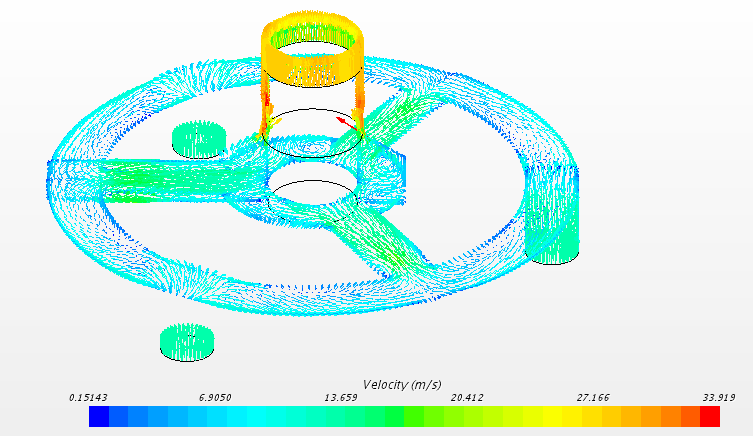
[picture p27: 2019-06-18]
2018-2019 Capstone documentation/Class papers and presentations/Images of Standy stuff/CFD_Velocity.PNG

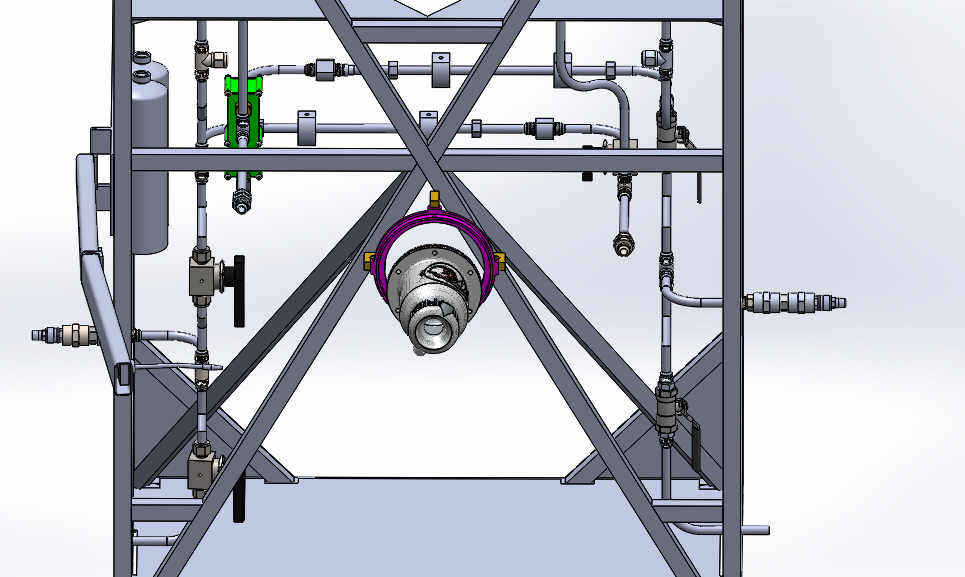
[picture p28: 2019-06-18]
2018-2019 Capstone documentation/Class papers and presentations/Images of Standy stuff/LMTS_5 lower section.JPG

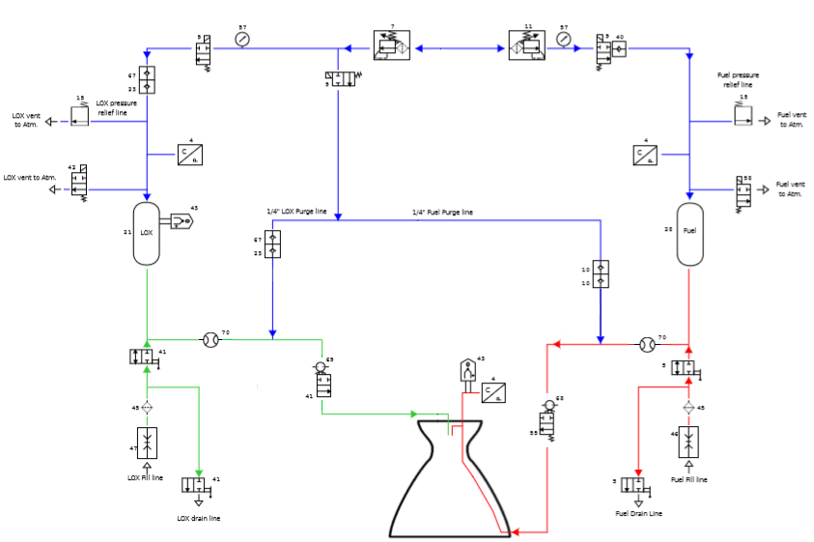
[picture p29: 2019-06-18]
PID/PID-system-overview-6-15-2019.png

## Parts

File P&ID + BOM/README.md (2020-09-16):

# P&ID

  This section contains drawings that outline the major components that the test stand consists of. It is seperated into the engine system, LOX system, fuel system, and pressure panel system.
  
  ## Documentation
    
   ### Archive
   
    This folder contains all previous versions of the PID. Work began in 2015/2016, with major revisions in 2018, 2019, 2020.

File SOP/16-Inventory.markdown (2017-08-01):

---
title: Inventory
layout: base
---

# Inventory

## Things that the group should have at least one of

 - First aid kit, trauma kit if possible
 - Jumper Cables
 - Extra water, Ice if possible for heat stroke

## Primary Tools & Supplies

### Hand Tools

  - box-wrenches
  - ignition wrenches
  - socket set
  - socket extensions
  - Adapter to connect automotive socket to right angle drill
  - automotive sockets (for sand-screws)
  - breaker bar (1/2 automotive type)
  - crescent wrenches (assorted sizes)
  - normal hammer
  - rubber mallet
  - mini-sledge hammer
  - screw drivers
  - security screw driver bit set
  - pliers
  - vise grips
  - snap ring pliers (for motor retainment rings if necessary)
  - allen wrench sets
  - box cutter  
  - Level (should be perminently in tower box)
  - measuring tape
  - strap wrenches for motor assembly
  - scissors
  - sheet metal shears
  - small hand-mirror on wand (for viewing LED colors on rail-side of rocket)
  - tool belt
  - philips quick-insert hex bits
  - hex bit extensions
  - hex bit to socket adaptors (1/4, 3/8, 1/2)
  - calipers
  - leather work-gloves

### Power Tools
  - DeWalt Right Angle Drill for driving in sand screws
  - 120VAC generator (for generator->tools, needed during tower setup)
  - cordless drill (with extra battery and charger)

### Support Tools 
  - saw horses (4)
  - Little Giant Ladder
  - 75lb digital postal scale (final weight of rocket necessary)
  - digital hanging fish scale (final weight of rocket necessary)
  - digital jewelers scale
  - (3) orange safety cones for top of sand screws
  - 100ft Extension cord
  - paint pole (for GoPro camera at tower)
  
### Support Supplies
  - cardboard PSAS sign to post by road
  - super-lube, for motor assembly
  - fire extinguisher
  - shovel (for fire duty)
  - hatchet (for brush)
  - first aid kit
  - 1/8 inch dia dowels, 3-4 ft long, for holding igniters in place in pyros (or small square balsa wood lengths)
  - E-matches 
  - 3-in-1 oil
  - WD-40
  - electrical tape
  - duct tape
  - safety glasses
  - zip ties
  - blue masking tape
  - Motor removal 2x4 kit (should be in one of the plastic tubs)
  - latex gloves, used during motor assembly/gluing/greesing
  - gasoline (if bringing dirt bikes), 5 gallons
  - 1/4in or 5/16in dowels, handy for a variety of things...
  - big trash bags
  - a tarp
  - A few Misc 2x4s and 4x4s (just in case)
  - card tables and chairs
  - narrow string/rope
  - ear plugs
  - rubber bands

## Emergency Tools & Supplies
  - orbital sander
  - dremmel tool
  - sae tap/die set
  - 4 inch angle grinder
  - sawzall
  - sand paper
  - hand sanding block
  - super glue
  - 5 min epoxy
  - 30 minute epoxy (may be needed for epoxying aerotech motor grains)
  - jb-weld
  - full drill bit set
  - 1/2 inch corded drill
  - hack saw
  - metal files
  - counter sinks
  - deburing tool
  - lighter

## Launch Tower Parts
  - blast shield
  - launch tower tub, which should include at least the following:
    - -(3) sets of guy wires
    - -(4) sand screws
  - launch tower electrical tub
    - -With long orange wires for igniter and safety boxes
    - -RF feed-line for tower computer to antenna
  - tower computer
  - 12v batteries for tower computer
  - solar panel for tower computer
  - antenna bar for tower
  - launch rail
  - tower top section
  - tower bottom section
  - tower base
  - Ropes and pulleys and such to raise and lower the rail
  - Launch rail teather to rocket
  - Umbilical Bar
  - high-visibility coverings for guy-wires

## Motor
  - Motor Casing
  - Forward and Aft Closures
  - Main fuel grains
  - Smoke Grain
  - O-rings
  - Special motor tools, if necessary
  - Igniters
  - 1/8 inch dowels
  - Grain removial 2x4
  - Plastic trash bag for burned liner (it smells really bad)

## Electrical Tools and Supplies
  - Dell LCD Monitor w/ S-Video and composite input (with external power supply)
  - JTAG adaptor
  - USB Cables
  - USB hub w/ power supply and mini-usb cable
  - Multi Meter
  - Soldering Iron
  - Resistor assortment
  - 12volt to 120VAC inverter w/ 12v battery clamps
  - 120vac to multi-voltage output AC wall wart adapters (2)
  - car usb charger
  - 12v car battery, if available
  - 4 channel Agelent Oscilloscope
  - AA batteries
  - AAA batteries
  - D batteries
  - 9v Batteries

## Cables
  - Roll Control launch detect shorting tether.
  - Opal docking station and FTDI cable.
  - TeleMetrum receive cable and antenna (multiple okay)
  - ARTS data cable (LEDs, USB Serial Adaptor)

## General Stuff
  - screw/nut/bolt assortments
  - Binoculars
  - 1200fps camera

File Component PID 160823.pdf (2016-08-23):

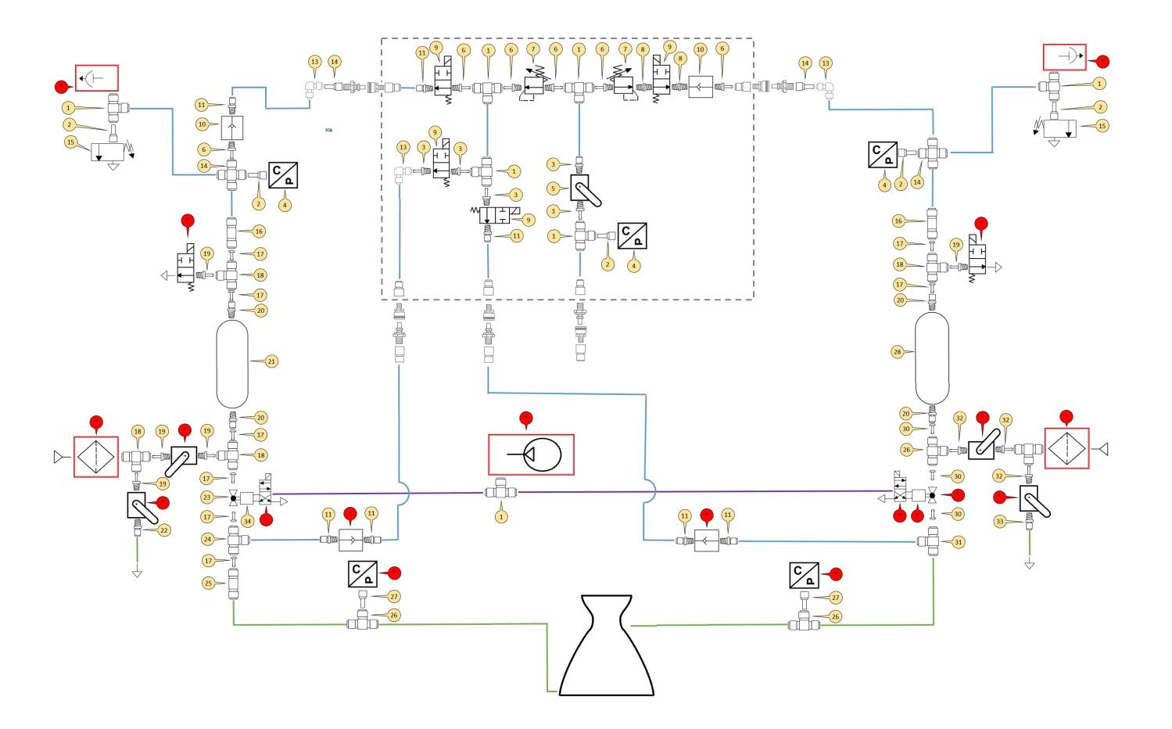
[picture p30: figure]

BOM Number | Part | Price | Part Count | Cost | Distributor | Part #
1 | 1/4" Ferrule Tee | $23.40 | | $0.00 | Swagelok | SS-400-3
2 | 1/4" Tube OD 1/4" NPT Female Tube Adapter | $10.15 | | $0.00 | Swagelok | SS-4-TA-7-4
3 | 1/4" Tube OD to 1/2" NPT Male Tube Adapter | | | $0.00 | Swagelok | SS-4-TA-1-8
4 | Pressure Transducer (3000 psi) | $188.75 | | $0.00 | Ashcroft / Grainger | G17M0215F23000
5 | Manual SS 316 1/2" NPT Ball Valve | $42.80 | | $0.00 | Sharpe Valves | SV39036TE004
6 | 1/4" NPT Male Tube Adapter | $6.32 | | $0.00 | Swagelok | SS-4-TA-1-4
7 | Two Stage Pressure Regulator w/ internal filter | $523.86 | | $0.00 | Swagelok | KCY1JRA412A20000
8 | 1/4" NPT Hex Nipple | $6.32 | | $0.00 | Swagelok | SS-4-HN
9 | Solenoids (Nitrogen) | $98.10 | | $0.00 | Asco | 8262H080
10 | Check Valves | $48.55 | | $0.00 | Swagelok | SS-4C4-1
11 | 1/4" Ferrule to 1/4" NPT Male Connector | $7.35 | | $0.00 | Swagelok | SS-400-1-4
12 | 90° Ferrule Union Elbow | | | | Swagelok | SS-400-9
13 | 1/4" Tube OD to 1/2" NPT Female Tube Adapter | | | | Swagelok | SS-4-TA-7-8
14 | 1/4" Ferrule Cross | $42.54 | | $0.00 | Swagelok | SS-400-4
15 | Relief Valves | $151.49 | | $0.00 | Swagelok | SS-4R3A5-SETB
16 | 1/4" to 1/2" Ferrule Union | | | | Swagelok | SS-810-6-4
17 | 1/2" Port Connector | | | | Swagelok | SS-811-PC
18 | 1/2" Ferrule Union Tee | | | | Swagelok | SS-810-3
19 | 1/2" NPT Male Tube Adapter | | | | Swagelok | SS-8-TA-1-8
20 | 1/2" Ferrule to 3/4" NPT Male Connector | | | | Swagelok | SS-810-1-12
21 | LOX Tank | $372.94 | | $0.00 | Hoke / eBay | 8HD4G
22 | 1/2" Ferrule to 1/2" NPT Male Connector | | | | Swagelok | SS-810-1-8
23 | Cryogenic Ball Valve | $150.28 | | $0.00 | Flowserve | C4466PMSE
24 | 1/2" to 1/4" Reducing Ferrule Union Tee | | | | Swagelok | SS-810-3-8-4
25 | 1/2" to 3/8" Reducing Ferrule Union | | | | Swagelok | SS-810-6-6
26 | 3/8" Ferrule Union Tee | | | | Swagelok | SS-600-3
27 | 3/8" NPT Female Tube Adapter | $10.15 | | $0.00 | Swagelok | SS-6-TA-7-6
28 | Ethanol Tank | $132.99 | 1 | $132.99 | Luxfer / Amazon | C020
29 | 3/8" Ferrule to 3/4" NPT Male Connector | | | | Swagelok | SS-600-1-12
30 | 3/8" Port Connector | | | | Swagelok | SS-601-PC
31 | 3/8" to 1/4" Reducing Ferrule Union Tee | | | | Swagelok | SS-600-3-6-4
32 | 3/8" Tube OD to 3/8" NPT Male Tube Adapter | | | | Swagelok | SS-6-TA-1-6
33 | 3/8" Ferrule to 3/8" NPT Male Connector | | | | Swagelok | SS-600-1-6
34 | Pneumatic Actuator - Worcester Double Acting 2539 | | | | Worcester | 25-_-39-_

Total

Manufactuer /

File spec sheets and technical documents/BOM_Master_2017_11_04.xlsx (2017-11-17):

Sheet: Test Stand Full BOM
 | LFETS BOM | Status | Spec Sheet Saved? | Progress Limiting? | Part # | Price | Qty | Total Cost | Manufacturer / Distributor | Spec Link | PID Ref # | Description | Notes (Include Location)
Engine | engine fuel port/flexline fitting | Not Spec'd |  | Yes |  |  |  |  |  |  |  | ethanol line to printed engine
Engine | Fitting | Not Spec'd |  | Yes |  |  |  |  |  |  |  | connects printed engine to fuel line
Engine | Injector/flexline fitting | Not Spec'd |  | Yes |  |  |  |  |  |  |  | lox line to engine injector
Igniter | Body V2 | Not Spec'd |  | Yes | Custom Printed Sintered Stainless | TBD | 1 |  | Shapeways |  | 51 | Not yet designed
Igniter | Fuel Orifice | Not Spec'd |  | No |  |  | 1 |  |  |  |  |  | TBD by pressure budget calcs
Igniter | Fuel Pressure Tank | Not Spec'd |  | No |  |  | 1 |  |  |  |  |  | Small press tank for bench testing
Igniter | Fuel Tank | Not Spec'd |  | No |  |  | 1 |  |  |  |  |  | Ethanol tank for bench testing
Igniter | GOX Tank | Not Spec'd |  | No |  |  | 1 |  |  |  |  |  | Small GOX tank for bench testing
Igniter | Igniter hose | Not Spec'd |  | Yes | 4468K131 |  | TBD |  | McMaster-Carr | https://www.mcmaster.com/#4468k131/=16wtdld |  | 3/16 ID - 1/8 to 18 Brass NPT with PTFE Lengths 12 to 240 inches Temp from -65 to 450 F max 3000 psi
Igniter | Pressure Sensor | Not Spec'd |  | No |  |  | 1 |  |  |  |  | ~200psi for testing, >500 for stand
Igniter | Regulators | Not Spec'd |  | No |  |  | 2 |  |  |  |  |  | Fuel press and GOX regulators
Pressure Panel | Misc | Spec'd/Not Ordered | Yes | Yes | Regulator 1000 psi | $90.00 | 1 | $90.00 | SwageLok | https://www.swagelok.com/downloads/WebCatalogs/en/MS-02-230.PDF | 11 | Pressure Regulator 1000 psi min, fuel side | KPP 1 L* N* A* 4 2 2 P* 2 0 0 0 0 (* denotes minimum value or option for functionality)
Test Stand | Consumables | Not Spec'd |  | No | Nitrogen K-Bottle |  | 1 | $0.00 |  |  | 50 | Nitrogen K-Bottle
Test Stand | Consumables | Not Spec'd |  | No | 1/8" diameter, long ramrod/stick/wire for LOX cleaning of pipes |  | 1 |  | Swagelok |  |  | We will need a ramrod or wire to clean the inside of the LOX piping. We will use the rod to push kimtech wipes through the piping during LOX cleaning.
Test Stand | Consumables | Not Spec'd |  | Defer | IPA (70% by volume) |  |  | $0.00 |  |  |  | Ethanol (70% by volume)
Test Stand | Misc | Not Spec'd |  | Defer | Cryo Insulation |  |  | $0.00 |  | http://www.rhhfoamsystems.com/high_density.php OR http://www.dunmore.com/products/cryogenic-insulation.html OR https://csabg.org/insulation/ |  | Cryo Insulation
Test Stand | Misc | Not Spec'd |  | Defer | Fuel Pump for loading ethanol |  | 1 | $0.00 |  |  |  | Fuel Pump for loading ethanol
Test Stand | Misc | Not Spec'd |  | No | Metal for machining parts - what kind? For what? |  |  | $0.00 |  |  |  | Metal for machining parts - what kind? For what?
Test Stand | Misc | Not Spec'd |  | Yes | Sheet metal for brackets |  |  | $0.00 |  |  |  | Sheet metal for brackets
Test Stand | NPT Thread Tape | Not Spec'd |  | Yes | NPT tape or sealant |  |  |  |  |  |  | 1/4", LOX/GOX-safe NPT thread tape | Should be suitable for cryo temps
Test Stand | Piping | Not Spec'd |  | Yes | Hosing |  | multiple |  |  | check mcmaster car for high pressure hosing |  | Hosing | Need hosing of the following lengths (in inches) - 12, 9.5, 11, 18, 7, 7 (check solidworks model for diameters
Test Stand | Regulators | Not Spec'd |  | No |  |  | 1 |  |  |  | 66 | Regulator for pnumatic actuator
Test Stand | Valve | Not Spec'd |  | Yes | HPRV-500-(pressure) | $113.00 | 2 | $113.00 |  | http://www.generant.com/hprv.shtml | 15 | High Pressure Relief Valve - 1/2 inch
Test Stand | Valve | Not Spec'd |  | Yes | LOX compatible check valve |  | 3 |  |  |  | 23 | M/M lox compatable check valve
Test Stand | Valve | Not Spec'd |  | Yes | Servo Motor Ball Valve Assembly |  | 1 | $0.00 |  |  | 56 | See main fuel valve project MFV
Test Stand | Valve | Not Spec'd |  | Yes | LOX compatible check valve |  | 3 |  |  |  | 67 | F/F lox compatable check valve
Test Stand | Valve Assembly | Not Spec'd |  | Yes | Main Fuel Valve |  | 1 |  | In house project |  | 68 | Main Fuel Valve - Electrically actuated Ball valve assembly
Test Stand | Valve Assembly | Not Spec'd |  | Yes | Main LOX valve |  | 1 |  | In house project |  | 69 | Main LOX Valve - Electrically actuated Ball valve assembly
Engine | Flex line to engine | Received/Have |  | Yes | 5425T93 (1 ft long) (1/2" dia) | $165.78 | 2 | $331.56 | McMaster-Carr | 5425T93 (https://www.mcmaster.com/) |  | 2 x 1-foot long, 1/2" diamter flex lines to connect to the engine fuel port and engine injector
Igniter | Body V1 | Received/Have |  | Yes | Machined Brass Round Bar | $13 | 1 |  |  |  | 51 | Machined, mofos!
Igniter | Check Valves | Received/Have |  | Yes | B-2C-1 | $26.19 | 2 | $52.38 | Swagelok | https://www.swagelok.com/en/catalog/Product/Detail?part=B-2C-1 |  |  | Either model is fine
Igniter | Controller | Received/Have |  | No | Arduino Uno | $24 | 1 |  | Arduino |  |  | Controls relay board
Igniter | Fitting | Received/Have |  | No | B-200-R-8 | $10.15 | 2 | $20.30 | Swagelok | https://www.swagelok.com/en/catalog/Product/Detail?part=B-200-R-8 | 13 | Reducer, 1/8 in. Tube OD x 1/2 in. Tube OD - Tube Fitting
Igniter | Fitting | Received/Have |  | No | B-200-3 | $9.84 | 3 |  | Swagelok | https://www.swagelok.com/en/catalog/Product/Detail?part=B-200-3 | 61 | 1/8 uniont tee
Igniter | Fitting | Received/Have |  | No | 50785K272 | $5.96 | 6 |  | McMaster-Carr | https://www.mcmaster.com/#50785k272/=17r7k8g | 62 | 1/8 bulkhead fitting
Igniter | Fitting | Received/Have |  | No | B-200-9 | $8.39 | 14 |  | Swagelok | https://www.swagelok.com/en/catalog/Product/Detail?part=B-200-9 | 63 | 1/8 elbo
Igniter | Fitting | Received/Have |  | No | B-400-R-2 | $3.94 | 4 |  | Swagelok | https://www.swagelok.com/en/catalog/Product/Detail?part=B-400-R-2 | 64 | 1/4 tube to 1/8 reducer
Igniter | Fitting | Received/Have |  | No | B-200-6 | $5.08 | 4 |  | Swagelok | https://www.swagelok.com/en/catalog/Product/Detail?part=B-200-6 | 65
Igniter | Fuel Filter | Received/Have |  | Yes | B-2F-7 | $30.85 | 1 | $30.85 | Swagelok | https://www.swagelok.com/en/catalog/Product/Detail?part=B-2F-7 |  | 7 micron filter
Igniter | Igniter Fittings | Received/Have |  | No | SS-200-1-OR | 14.08 | 4 | $56.32 | Swagelok | https://www.swagelok.com/en/catalog/Product/Detail?part=SS-200-1-OR | - | Male O-Seal Connector, 1/8 in. Tube OD x 5/16-24 Male O-Seal SAE/MS Straight Thread, Tube Fitting
Igniter | Orifice Fittings | Received/Have |  | No | B-200-7-2 | $4.56 | 2 | $9.12 | Swagelok | https://www.swagelok.com/en/catalog/Product/Detail?part=B-200-7-2 | - | 1/8" FNPT to 1/8" Swagelok
Igniter | Relays | Received/Have |  | No | 4ch, 5V relay board | $8.98 | 1 |  | Generic |  |  | Controls solenoids/spark power
Igniter | Sol. Valve Fittings | Received/Have |  | No | B-200-1-2 | $3.42 | 16 | $54.72 | Swagelok | https://www.swagelok.com/en/catalog/Product/Detail?part=B-200-1-2 | 53 | 1/8"-27 NPT Swagelok | Two separate orders; recieved 10/16 as of 6/6/2017
Igniter | Solenoid Valves | Received/Have | Yes | Yes | D2011-SB5-T-TO-LC-C203 | $71.00 | 5 | $355.00 | Gems | http://ecatalog.gemssensors.com/ecatalog/configurators/ABCD/D2011 | 49 | https://drive.google.com/open?id=0BzZpualyKAXnLS1nNEk2MTB1TzA | Not on Spec Sheet: Max operating pressure is 900 PSI. Min order of 5 - get LOX cleaned, works for both LOX and Ethonal side of Igniter, will end up with 3 spare
Igniter | Spark Plug | Received/Have |  | Yes | CM-6 | $7.87 | 1 |  | NGK |  |  | M10x1.0 thread
Igniter | Spark Regulator | Received/Have |  | No | Servo Tester | $6.85 | 1 |  | Generic |  |  | PWM signal generator
Igniter | Spark System | Received/Have |  | Yes | A-02 6-12V | $50.00 | 1 |  | RCEXL |  |  | Ignition coil, from RC engine
Igniter | Tubing | Received/Have |  | Yes | 1/8" -------- Tubing | $49.16 | 2 | $98.32 | McMaster-Carr | https://www.mcmaster.com/#89785k811/=17sefr1
MFV - G | 1/4 in Hub | Received/Have |  | No | 12488 | $4.99 | 1 | $4.99 | Sparkfun | https://www.sparkfun.com/products/12488
MFV - G | 20A relay | Received/Have |  | No | 10924 | $2.95 | 1 | $2.95 | Sparkfun | https://www.sparkfun.com/products/10924
MFV - G | 6ft USB cable | Received/Have |  | No | 512 | $3.95 | 2 | $7.90 | Sparkfun | https://www.sparkfun.com/products/512
MFV - G | 6mm Hub | Received/Have |  | No | 12318 | $4.99 | 1 | $4.99 | Sparkfun | https://www.sparkfun.com/products/12318
MFV - G | Al Chanel 1.5" | Received/Have |  | No | 12383 | $2.99 | 2 | $5.98 | Sparkfun | https://www.sparkfun.com/products/12383
MFV - G | Alagator clip/pitgtail | Received/Have |  | No | 13191 | $2.95 | 2 | $5.90 | Sparkfun | https://www.sparkfun.com/products/13191
MFV - G | Arduino Uno | Received/Have |  | No | 11021 | $24.95 | 2 | $49.90 | Sparkfun | https://www.sparkfun.com/products/11021
MFV - G | DC Motor | Received/Have |  | Yes | 638263 | $39.99 | 1 | $39.99 | Servo City | https://www.servocity.com/12-rpm-hd-premium-planetary-gear-motor |  | 12V, torque 506 in lb, Stall current 20A | https://www.servocity.com/files/index/download/id/1455654116/
MFV - G | F/F Jumper wires | Received/Have |  | No | 8430 | $3.95 | 2 | $7.90 | Sparkfun | https://www.sparkfun.com/products/8430
MFV - G | H-Bridge | Received/Have |  | No | 315 | $2.35 | 1 | $2.35 | Sparkfun | https://www.sparkfun.com/products/315
MFV - G | Input Board | Received/Have |  | Yes | 605120 | $0.99 | 1 | $0.99 | Servo City | https://www.servocity.com/gear-motor-input-board-d |  | Power adapter thingy to make it pluggable
MFV - G | M/F Jumper wires | Received/Have |  | No | 9140 | $3.95 | 2 | $7.90 | Sparkfun | https://www.sparkfun.com/products/9140
MFV - G | M/M Jumper wires | Received/Have |  | No | 10897 | $24.95 | 1 | $24.95 | Sparkfun | https://www.sparkfun.com/products/10897
MFV - G | Motor Mount | Received/Have |  | Yes | 555174 | $4.99 | 1 | $4.99 | Servo City | https://www.servocity.com/premium-planetary-gear-motor-mount
MFV - S | Battery | Received/Have |  | Yes | 2225 | $17.29 | 1 | $17.29 | Polulu | https://www.pololu.com/product/2225. |  | 7.2 V rechargable battery pack | https://www.pololu.com/file/download/2374-servo-horn-dimensions.pdf?file_id=0J760
MFV - S | Servo | Received/Have |  | Yes | 2375 | $59.95 | 1 | $59.95 | Polulu | https://www.pololu.com/product/2375/specs |  | Servo with 35 in lb torque 7.4 V | https://www.pololu.com/file/0J706/HD-1235MG.pdf
MFV - S | Servo Horn | Received/Have |  | Yes | 2374 | $8.95 | 1 | $8.95 | Polulu | https://www.pololu.com/product/2374 |  | Horn for linkage
Pressure Panel | Fitting | Received/Have | Yes | No | B-400-3 | 9.94 | 6 | $59.64 | Swagelok | https://www.swagelok.com/en/catalog/Product/Detail?part=B-400-3 | 1 | Union Tee, 1/4 in. Tube OD - Tube Fitting | Received 3/20/17
Pressure Panel | Fitting | Received/Have |  | No | B-4-TA-1-8 | $6.01 | 1 | $6.01 | Swagelok | https://www.swagelok.com/en/catalog/Product/Detail?part=B-4-TA-1-8 | 3 | Male Tube Adapter, 1/4 in. Tube OD x 1/2 in. Male NPT - Tube Fitting | Received 3/20/17
Pressure Panel | Fitting | Received/Have |  | No | B-4-TA-1-4 | $3.52 | 8 | $28.16 | Swagelok | https://www.swagelok.com/en/catalog/Product/Detail?part=B-4-TA-1-4 | 6 | Male Tube Adapter, 1/4 in. Tube OD x 1/4 in. Male NPT - Tube Fitting
Pressure Panel | Fitting | Received/Have |  | No | B-4-HN | $4.04 | 16 | $64.64 | Swagelok | https://www.swagelok.com/en/catalog/Product/Detail?part=B-4-HN | 8 | Hex Nipple, 1/4 in. Male NPT - Pipe Fitting | 7 additional need to be ordered; 1 was Received 3/20/17
Pressure Panel | Fitting | Received/Have |  | No | B-400-9 | $6.84 | 5 | $34.20 | Swagelok | https://www.swagelok.com/en/catalog/Product/Detail?part=B-400-9 | 12 | Union Elbow, 1/4 in. Tube OD - Tube Fitting | Received 3/20/17
Pressure Panel | Fitting | Received/Have |  | No | 50785K273 | $8.23 | 4 | $32.92 | McMaster-Carr | https://www.mcmaster.com/#50785k273/=16jngry | 25 | Through-Wall Adapter, 1/4 NPT Female, 3/4"-16 UNF Male
Pressure Panel | Fitting | Received/Have |  | No | B-400-1-4 | $3.01 | 6 | $18.06 | Swagelok | https://www.swagelok.com/en/catalog/Product/Detail?part=B-400-1-4 | 37 | Male Connector, 1/4 in. Tube OD x 1/4 in. Male NPT - Tube Fitting | Received 3/20/17
Pressure Panel | Fitting | Received/Have |  | No | B-400-1-8 | $6.01 | 1 | $6.01 | Swagelok | https://www.swagelok.com/en/catalog/Product/Detail?part=B-400-1-8 | 38 | Male Connector, 1/4 in. Tube OD x 1/2 in. Male NPT - Tube Fitting | Received 3/20/17
Pressure Panel | Fitting | Received/Have |  | No | B-400-3-4TTF | 12.22 | 2 | $24.44 | Swagelok | https://www.swagelok.com/en/catalog/Product/Detail?part=B-400-3-4TTF | 44 | Female Branch Tee, 1/4 in. Tube OD x 1/4 in. Tube OD x 1/4 in. Female NPT - Tube Fitting | Currently in Model, not sure if we already have or what the status. (connected to pressure dial)
Pressure Panel | Fitting | Received/Have |  | No | B-4-HCG | 6.21 | 2 | $12.42 | Swagelok | https://www.swagelok.com/en/catalog/Product/Detail?part=B-4-HCG | 52 | Hex Coupling, 1/4 in. Female NPT, Tube Fitting
Pressure Panel | Fitting | Received/Have |  | No | B-4-TA-7-4 | $3.21 | 1 | $3.21 | Swagelok | https://www.swagelok.com/en/catalog/Product/Detail?part=B-4-TA-7-4 | 54 | Female Tube Adapter, 1/4 in. Tube OD x 1/4 in. Female NPT - Tube Fitting
pressure Panel | Fitting | Received/Have |  | No | B-400-4 | $15.53 | 2 |  | Swagelok | https://www.swagelok.com/en/catalog/Product/Detail?part=B-400-4 | 59 | 1/4 union cross
Pressure Panel | Misc | Received/Have |  | Yes | KCY1JRA412A20000 | $525.00 | 1 | $525.00 |  |  | 7 | Pressure Regulator
Pressure Panel | Misc | Received/Have |  | No | SSQF4B4PM | 32.61 | 2 | $65.22 | Swagelock | https://www.swagelok.com/en/catalog/Product/Detail?part=SS-QF4-B-4PM | 46 | Quick disconnect
Pressure Panel | Misc | Received/Have |  | No | SSQF4S4PM | 13.15 | 2 | $26.30 | Swagelock | https://www.swagelok.com/en/catalog/Product/Detail?part=SS-QF4-S-4PM | 47 | Quick disconnect
Pressure Panel | Misc | Received/Have |  | Yes | PFP663ZRR1 | 40 | 2 | $80.00 | Winters | http://winters.com/wp-content/uploads/PFP.pdf | 57 | Winters 600 PSI Pressure Gauge | We should check the fittings for this
Test Stand | Fitting | Received/Have | Yes | No | B-8-TA-7-4 | $6.01 | 5 | $30.05 | Swagelok | https://www.swagelok.com/en/catalog/Product/Detail?part=B-8-TA-7-4 | 2 | Female Tube Adapter, 1/2 in. Tube OD x 1/4 in. Female NPT - Tube Fitting
Test Stand | Fitting | Received/Have |  | No | B-4-HN | $4.04 | 11 | $44.44 | Swagelok | https://www.swagelok.com/en/catalog/Product/Detail?part=B-4-HN | 8 | Hex Nipple, 1/4 in. Male NPT - Pipe Fitting | Received 3/20/17
Test Stand | Fitting | Received/Have |  | No | B-400-9 | $6.84 | 4 | $27.36 | Swagelok | https://www.swagelok.com/en/catalog/Product/Detail?part=B-400-9 | 12 | Union Elbow, 1/4 in. Tube OD - Tube Fitting | Received 3/20/17
Test Stand | Fitting | Received/Have |  | No | B-810-4 | $23.81 | 4 | $95.24 | Swagelok | https://www.swagelok.com/en/catalog/Product/Detail?part=B-810-4 | 14 | Union Cross, 1/2 in. Tube OD - Tube Fitting
Test Stand | Fitting | Received/Have |  | No | 50785K275 | $16.59 | 8 | $132.72 | McMaster-Carr | https://www.mcmaster.com/#50785k275/=16jn22t | 16 | Through-Wall Adapter, 1/2 NPT x 1-1/8"-14 UNF
Test Stand | Fitting | Received/Have |  | No | B-810-9 | $13.25 | 11 | $145.75 | Swagelok | https://www.swagelok.com/en/catalog/Product/Detail?part=B-810-9 | 17 | Union Elbow, 1/2 in. Tube OD - Tube Fitting | Received 3/20/17
Test Stand | Fitting | Received/Have |  | No | B-810-3 | $18.22 | 15 | $273.30 | Swagelok | https://www.swagelok.com/en/catalog/Product/Detail?part=B-810-3 | 18 | Union Tee, 1/2 in. Tube OD - Tube Fitting | Received 3/20/17
Test Stand | Fitting | Received/Have |  | No | B-8-TA-1-8 | $6.01 | 2 | $12.02 | Swagelok | https://www.swagelok.com/en/catalog/Product/Detail?part=B-8-TA-1-8 | 19 | Male Tube Adapter, 1/2 in. Tube OD x 1/2 in. Male NPT - Tube Fitting | Received 3/20/17
Test Stand | Fitting | Received/Have |  | No | B-810-1-12 | $12.01 | 2 | $24.02 | Swagelok | https://www.swagelok.com/en/catalog/Product/Detail?part=B-810-1-12RT | 20 | Male Connector, 1/2 in. Tube OD x 3/4 in. Male ISO Tapered Thread - Tube Fitting
Test Stand | Fitting | Received/Have |  | No | B-810-1-8 | $6.84 | 27 | $184.68 | Swagelok | https://www.swagelok.com/en/catalog/Product/Detail?part=B-810-1-8 | 22 | Male Connector, 1/2 in. Tube OD x 1/2 in. Male NPT - Tube Fitting | Received 3/20/17, Recieved 6 more on 6/6 but this seems to already reflect that
Test Stand | Fitting | Received/Have |  | No | B-810-2-8 | $10.67 | 7 | $74.69 | Swagelok | https://www.swagelok.com/en/catalog/Product/Detail?part=B-810-2-8 | 24 | Male Elbow, 1/2 in. Tube OD x 1/2 in. Male NPT - Tube Fitting | Received 3/20/17
Test Stand | Fitting | Received/Have |  | No | 50785K273 | $8.23 | 4 | $32.92 | McMaster-Carr | https://www.mcmaster.com/#50785k273/=16jn0zr | 25 | Through-Wall Adapter, 1/4 NPT Female, 3/4"-16 UNF Male
Test Stand | Fitting | Received/Have |  | No | B-4-ME | $8.70 | 6 | $52.20 | Swagelok | https://www.swagelok.com/en/catalog/Product/Detail?part=B-4-ME | 26 | Male Elbow, 1/4 in. Male NPT - Pipe Fitting
Test Stand | Fitting | Received/Have |  | No | B-4-SE | $11.49 | 2 | $22.98 | Swagelok | https://www.swagelok.com/en/catalog/Product/Detail?part=B-4-SE | 27 | Street Elbow, 1/4 in. Female NPT x 1/4 in. Male NPT - Pipe Fitting
Test Stand | Fitting | Received/Have |  | No | B-810-8-8 | $16.05 | 2 | $32.10 | Swagelok | https://www.swagelok.com/en/catalog/Product/Detail?part=B-810-8-8 | 29 | Female Elbow, 1/2 in. Tube OD x 1/2 in. Female NPT - Tube Fitting
Test Stand | Fitting | Received/Have | Yes | No | B-12-HRN-8 | $11.18 | 2 | $22.36 | Swagelok | https://www.swagelok.com/en/catalog/Product/Detail?part=B-12-HRN-8 | 30 | Hex Reducing Nipple, 3/4 in. Male NPT x 1/2 in. Male NPT - Pipe Fitting | Received 3/20/17
Test Stand | Fitting | Received/Have |  | No | B-810-3-8TMT | $18.43 | 1 | $18.43 | Swagelok | https://www.swagelok.com/en/catalog/Product/Detail?part=B-810-3-8TMT | 31 | Male Run Tee, 1/2 in. Tube OD x 1/2 in. Male NPT x 1/2 in. Tube OD - Tube Fitting | Received 3/20/17
Test Stand | Fitting | Received/Have |  | No | B-810-1-4 | $7.15 | 1 | $7.15 | Swagelok | https://www.swagelok.com/en/catalog/Product/Detail?part=B-810-1-4 | 32 | Male Connector, 1/2 in. Tube OD x 1/4 in. Male NPT - Tube Fitting
Test Stand | Fitting | Received/Have |  | No | B-810-3-8TTF | $19.77 | 2 | $39.54 | Swagelok | https://www.swagelok.com/en/catalog/Product/Detail?part=B-810-3-8TTF | 33 | Female Branch Tee, 1/2 in. Tube OD x 1/2 in. Tube OD x 1/2 in. Female NPT - Tube Fitting
Test Stand | Fitting | Received/Have |  | No | B-8-ST | $28.67 | 1 | $28.67 | Swagelok | https://www.swagelok.com/en/catalog/Product/Detail?part=B-8-ST | 34 | Street Tee, 1/2 in. Female NPT x 1/2 in. Male NPT x 1/2 in. Female NPT - Pipe Fitting
Test Stand | Fitting | Received/Have |  | No | B-8-BT | $28.88 | 1 | $28.88 | Swagelok | https://www.swagelok.com/en/catalog/Product/Detail?part=B-8-BT | 35 | Branch Tee, 1/2 in. Female NPT x 1/2 in. Female NPT x 1/2 in. Male NPT - Pipe Fitting
Test Stand | Fitting | Received/Have |  | No | B-810-P | $4.14 | 2 | $8.28 | Swagelok | https://www.swagelok.com/en/catalog/Product/Detail?part=B-810-P | 36 | Plug for 1/2 in. Swagelok Tube Fitting | Received 3/20/17
Test Stand | Fitting | Received/Have |  | No | B-400-1-4 | $3.52 | 2 | $7.04 | Swagelok | https://www.swagelok.com/en/catalog/Product/Detail?part=B-400-1-4BT | 37 | Bored-Through Male Connector, 1/4 in. Tube OD x 1/4 in. Male NPT - Tube Fitting | Received 3/20/17
Test Stand | Fitting | Received/Have |  | No | B-400-1-8 | $6.01 | 2 | $12.02 | Swagelok | https://www.swagelok.com/en/catalog/Product/Detail?part=B-400-1-8 | 38 | Male Connector, 1/4 in. Tube OD x 1/2 in. Male NPT - Tube Fitting | Received 3/20/17
Test Stand | Fitting | Received/Have |  | No | B-810-5-8 | $44.28 | 1 | $44.28 | Swagelok | NA | 39 | 45° Male Elbow, 1/2 in. Tube OD x 1/2 in. Male NPT - Tube Fitting | Delivered 14 May 17
Test Stand | Instrumentation | Received/Have |  | Yes | Flow meter |  | 1 |  |  |  | 70 | Flow meter
Test Stand | Misc | Received/Have |  | Yes | 8HD4G | Have | 1 |  |  |  | 21 | LOX Tank
Test Stand | Misc | Received/Have |  | Yes | C020 | Have | 1 |  |  |  | 28 | Ethanol Tank
Test Stand | Misc | Received/Have |  | No | 98355K863 | 7.98 | 2 | $15.96 | McMaster-Carr | https://www.mcmaster.com/#98355k863/=16wxhkk | 45 | Micron Inline Filter
Test Stand | Misc | Received/Have |  | No | WCABR1003 |  | 1 |  |  | https://github.com/psas/liquid-engine-test-stand/blob/master/doc/Component_Spec_Sheets/Worcester%20Pneumatic%20Actuator.pdf | 48 | Pnumatic actuator
Test Stand | Piping | Received/Have |  | Yes | 1/2 Tubing, (SS316) | $48.30 | 5 | $241.50 | McMaster-Carr | https://www.mcmaster.com/#89785k843/=17seisy |  | Piping
Test Stand | Piping | Received/Have |  | Yes | 1/4 Tubing (SS316) | $63.09 | 2 | $126.18 | McMaster-Carr | https://www.mcmaster.com/#89785k819/=17seha8 |  | Piping
Test Stand | Valve | Received/Have |  | Yes | 4024T730 | $44.20 | 2 | $88.40 | McMaster-Carr | https://www.mcmaster.com/#4024t73/=16jnjcz | 5 | Ball Valve 1/2 NPT Female
Test Stand | Valve | Received/Have |  | No | B-4C4-1 | $25.05 | 2 | $50.10 | Swagelok | https://www.swagelok.com/en/catalog/Product/Detail?part=B-4C4-1 | 10 | Poppet Check Valve, Fixed Pressure, 1/4 in. FNPT, 1 psig (0.07 bar)
Test Stand | Valve | Received/Have |  | No | 46105K690 | $21.67 | 1 | $21.67 | McMaster-Carr | https://www.mcmaster.com/#46105k69/=16jni3l | 40 | Compact High-Pressure Backflow-Prevention Valve for Water, Brass Body, 1/4 NPTF Male
Test Stand | Valve | Received/Have | Yes | Yes | 05C47C-6666AT/NPT-LD | 375 | 3 | $1125.00 |  | https://drive.google.com/file/d/0BzKESZoHfv_oWXg5NktVZ0l1Zm8/view?usp=sharing | 41 | LOX compatable Ball Valve
Test Stand | Valve | Received/Have |  | Yes | E29LR62 | $631.38 | 1 | $631.38 | Magnatrol | http://www.magnatrol.com/lr_valve4.html | 42 | 12 V DCSOLENOID VALVE | Possibly SV39036TE004 instead - need to verify that this is ready to order
Test Stand | Valve | Received/Have |  | Yes | Sharpe 39036 |  | 1 | $0.00 |  |  | 55 | 1/2 in ball valve, main fuel valve
Test Stand | Valve | Received/Have | Yes | Yes | Fuel Vent Valve (solinoid) | 820 | 1 | $912.00 | Clark Cooper |  | 58 | Fuel Vent Valve (solinoid)
Consumables | LOX Cleaning Items | Spec'd/Not Ordered |  | No | Alcohol Wipes |  |  |  | Costco or Similar |  |  | Alcohol Wipes (for cleaning shoes before LOX handling)
Consumables | LOX Cleaning Items | Spec'd/Not Ordered |  | No | Cotton Swabs |  |  |  | Costco or Similar |  |  | Cotton Swabs - LOX Cleaning
Consumables | LOX Cleaning Items | Spec'd/Not Ordered |  | Defer | Dawn Soap |  |  |  | Costco or Similar |  |  | Dawn Soap - LOX Cleaning
Consumables | LOX Cleaning Items | Spec'd/Not Ordered |  | No | Distilled Water |  |  |  | Costco or Similar |  |  | Distilled Water - LOX Cleaning
Consumables | LOX Cleaning Items | Spec'd/Not Ordered |  | Defer | Heavy Duty Aluminum foil |  |  |  | Costco or Similar |  |  | Heavy Duty Aluminum foil - LOX Cleaning/Storage
Consumables | LOX Cleaning Items | Spec'd/Not Ordered |  | Defer | IPA (Acetone?) |  |  |  | Costco or Similar |  |  | IPA (Acetone?) - LOX Cleaning
Consumables | LOX Cleaning Items | Spec'd/Not Ordered |  | Defer | Ziplock Baggies (varying sizes) |  |  |  | Costco or Similar |  |  | Ziplock Baggies - LOX Cleaning/Storage
Engine | Pressure Transducer | Spec'd/Not Ordered |  | Yes | PX119-600GI | $99.00 | 1 | $99.00 | Omega | http://www.omega.com/pressure/pdf/PX119.pdf |  | Pressure transducer up to 600psi, 257 deg F and 20-500 Hz
Engine | Thermocouple | Spec'd/Not Ordered |  | Yes | DH-1-24-J-12 | $21.00 | 2 | $42.00 | Omega | http://www.omega.com/pptst/BARE_SH_DH_OV_ELEMENTS.html |  | 24 gauge, Double hole round insulated type J
Engine | Thermocouple Cement | Spec'd/Not Ordered |  | Yes | CC HIGH TEMP | $18.80 | 1 | $18.80 | Omega | http://www.omega.com/temperature/pdf/OB_BOND_CHEM_SET.pdf |  | High temp cement for thermocouples
igniter | Fuel Filter | Spec'd/Not Ordered |  | Yes | 98355K833 | $3.60 | 2 | $7.20 | McMaster-Carr | https://www.mcmaster.com/#98355k833/=19b9q0d |  | 90 micron filter
Ignition System | Red Button | Spec'd/Not Ordered |  | Defer | Giant Red Button |  | 1 |  | Ryan |  |  | Giant Red Button - Speak with Kristin | If not available, spec an old-timey dynamite plunger
Test Stand | Misc | Spec'd/Not Ordered |  | Yes | TDH40-B-G-1000-03-Q005 | $141.00 | 4 | $129.00 | Transducers Direc | http://www.transducersdirect.com/products/pressure-transducers/tdh40-pressure-transducer/ | 4 | Pressure Transducer | Fuel/Lox tank pressure regulated <1000psi
Pressure Panel | Misc | Spec'd/Not Ordered |  | Yes | TDH40-B-G-5000-03-Q005 | $141.00 | 1 | $129.00 | Transducers Direc | http://www.transducersdirect.com/products/pressure-transducers/tdh40-pressure-transducer/ | 4 | Pressure Transducer | N2 unregulated 5000psi
Pressure Panel | Misc | Spec'd/Not Ordered |  | No | b242407ch |  | 1 | $0.00 |  |  |  | Metal enclosure for Pressure Panel | Purchase from Automation direct. Call for quote
Pressure Panel | Valve | Spec'd/Not Ordered |  | Yes | 8262H019VDC12 | 53 | 3 | 159 |  | http://www.lesman.com/unleashd/catalog/valves/ASCO-valve-8262/ASCO-Valve-8262H-8263H-GP-spec-R3.pdf | 9 | ASCO 8262H019 12V DC | Purchase from asco or asco distributor
Safety | ABC Fire Extinguisher | Spec'd/Not Ordered | Not Available | Defer | 21008635N | $24.84 | 4 | $99.36 | Kidde / Walmart | https://www.walmart.com/ip/Full-Home-Fire-Extinguisher/42732926?wmlspartner=wlpa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 |  | Verify this must NOT be a water type fire extinguisher, or have another firefighting solution | This previousely called out a WATER (Type A) extinguisher. Water does not play well with LOX. Changed to type ABC. If Water is necessary, do fix this.
Safety | PPE | Spec'd/Not Ordered |  | Defer | Cryogenic Gloves Low Temperature Resistant LN2 Cold proof Nitrogen Protective Gloves Mid-Arm Size: L | $66.69 | 2 | $133.38 | Amazon | https://www.amazon.com/Cryogenic-Temperature-Resistant-Nitrogen-Protective/dp/B016UHDGRA?s=hi |  | Cryogenic Gloves (Standard: EN 511) rated to -360 degrees
Safety | PPE | Spec'd/Not Ordered |  | Defer | 2AUB7 | $34.60 | 2 | $69.20 | Grainger | https://www.grainger.com/product/CONDOR-Ratchet-Faceshield-Assembly-WP10998/_/N-azq/Ntt-face+shield+cryogenic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 |  | Polycarbonate Face Shield, 0.04" Thick, 7" Long
Safety | PPE | Spec'd/Not Ordered |  | Defer | 4EY97 | $1.09 | 2 (or more?) | $2.18 | Grainger | https://www.grainger.com/product/CONDOR-CONDOR-Uncoated-Wraparound-WP6930330/_/N-k2a?searchBar=true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 |  | CONDOR Uncoated Wraparound Safety Glasses, Polycarbonate Safety Glasses, Frameless, Clear, Universal Size
Safety | PPE | Spec'd/Not Ordered |  | Defer | 8URW2 | 7.92/pkg 10 | 2 pkg | 15.84 | Grainger | https://www.grainger.com/product/GRAINGER-APPROVED-33dB-Disposable-Bell-Shape-8URW2 |  | 33dB Disposable Bell-Shape Ear Plugs
Safety | PPE | Spec'd/Not Ordered |  | Defer | A02CRC24X36 |  | 2 |  | Spec'd Through Grainger, but Amazon has better prices | https://www.grainger.com/product/NATIONAL-SAFETY-APPAREL-Cryogenic-Apron-WP106015/_/N-j3dZ1yzgdy5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 |  | Cryogenic Apron (EN 511)
Safety | Safety | Spec'd/Not Ordered |  | Defer | Large stainless steel baking sheet/drip pan |  | 1 |  | Costco or Similar |  |  | Something to put under the LOX tank during filling so LOX doesn't spill & catch fire
Structure | Fasteners | Spec'd/Not Ordered |  | Yes | 30.2 | 2 | 60.4 | McMaster-Carr | https://www.mcmaster.com/#orders/=18trybt |  | Low Profile Strut Channel - 10 ft Red
Test Stand | Consumables | Spec'd/Not Ordered |  | Defer | Disposable Gloves, Latex Free? - S, M, & L |  |  |  | Costco
Test Stand | Consumables | Spec'd/Not Ordered |  | No | KimTech Clean Wipes | $2.29/280ct | 3 | 6.87 | Costco | https://www.costco.com/Kimtech-Cleaning-Wipes-280ct.product.11701512.html
Test Stand | Consumables | Spec'd/Not Ordered |  | No | Scientific Squirt Bottles? |  | 4 |  | Costco? |  |  | Squirt bottles for cleaning, 2 for distilled water, 2 for IPA
Test Stand | Consumables | Spec'd/Not Ordered |  | Defer | LOX, will be ordered from Praxair | $152.81 | 180 L | $152.81 | Praxair | PSU's Contact @ Praxair: Steve, work: 18007729247, cell: 3603342043 |  | LOX, will be ordered from Praxair, $102.81 for liquid, $38.00 duer rental (1 month), $12 hazmat charge
Test Stand | Load Cell | Spec'd/Not Ordered | Yes | No | SEN-10245 | 9.95 | 6 | 59.7 | Sparkfun | https://www.sparkfun.com/products/10245 | 60 | Load cells for tank mass & flow sensing | Also found in bathroom scales.
Test Stand | Thermocouple | Spec'd/Not Ordered | Yes | Yes | SEN-00251 | $13.95 | 2 | 27.9 | Sparkfun | https://www.sparkfun.com/products/251 | 43 | Temp sense for LOX tank
 |  |  |  | Defer | Hand engraver |  |  |  |  |  |  | For engraving things we don't want to put tags on
 |  |  |  | Defer | Tags |  |  |  |  |  |  | For Labeling Parts
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

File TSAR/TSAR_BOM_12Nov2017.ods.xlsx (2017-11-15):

Part Description | System | Type | Status | Spec Sheet Saved? | Part # | Price | QTY | Total Cost | Manufacturer/ Distributor | Spec Link | PID Ref# | Notes (Include location) | More Description | Communication Protocol | Connecter Type | Data Output Type | Word size (if digital) | Current supply requirements | Voltage Supply Requirements | Power | Measurement Range | Operating Pressure | Operating Temp | Electrical Notes
Pressure Transducer | Pressure Panel | Pressure Transducer | Spec'd/Not Ordered |  | TDH40 | $141.00 | 2 | $282.00 | Transducers Direc | http://www.transducersdirect.com/products/pressure-transducers/tdh40-pressure-transducer/ | 4 | Also need to buy the cables | Pressure Transducer | Analog | M12 | Analog |  | approx 3mA | 8 - 28VDC |  | 3 to 10,000 psi |  | -20 to 80C | For best performance use shielded cables.
Pressure Transducer | Test Stand | Pressure Transducer | Spec'd/Not Ordered |  | TDH40 | $141.00 | 3 | $423.00 | Transducers Direc | http://www.transducersdirect.com/products/pressure-transducers/tdh40-pressure-transducer/ | 4 | Also need to buy the cables | Pressure Transducer | Analog | M12 | Analog |  | approx 3mA | 8 - 28VDC |  | 3 to 10,000 psi |  | -20 to 80C | For best performance use shielded cables.
Automatic Valve | Pressure Panel | Valve | Spec'd/Not Ordered |  | 8262H019VDC12 | $53.00 | 3 | $159.00 | KSC Direct | http://www.lesman.com/unleashd/catalog/valves/ASCO-valve-8262/ASCO-Valve-8262H-8263H-GP-spec-R3.pdf | 9 | Purchase from asco or asco distributor | ASCO 8262H019 12V DC |  |  |  |  |  | 12VDC (maybe?) |  |  | 750 psi | -25 to 55C | Normally Closed (should be normally open)
Test Stand | Valve |  | Received/Have | Yes | E29LR62 | $631.38 | 1 | $631.38 | Magnatrol | http://www.magnatrol.com/lr_valve4.html | 42 |  | Possibly SV39036TE004 instead - need to verify that this is ready to order | N/A | Wires | N/A | N/A | 1 Amp hold/ 2.7 amp inrush | 120V/60 Hz | 45 AC/23DC |  |  |  | No specs for DC Operation
Type K Thermocouple | Test Stand | Thermocouple | Spec'd/Not Ordered | Yes | SEN-00251 | $13.95 | 5 | $69.75 | Sparkfun | https://www.sparkfun.com/products/251 | 43 |  | Type K Thermocouple for Temp sense for LOX tank |  | 30 Guage Stripped Wires |  |  |  |  |  | -270 to +1372C |  | -73 to +482C | Sparkfun: Works great with our Thermocouple Amplifier AD595 IC!
Igniter | Solenoid Valves |  | Received/Have | Yes | D2011-SB5-T-TO-LC-C203 | $71.00 | 5 | $355.00 | Gems | http://ecatalog.gemssensors.com/ecatalog/configurators/ABCD/D2011 | 49 | https://drive.google.com/open?id=0BzZpualyKAXnLS1nNEk2MTB1TzA | Min order of 5 - get LOX cleaned, works for both LOX and Ethonal side of Igniter, will end up with 3 spare | N/A | Wire (18" included) | N/A | N/A | .8333 A | 12VDC | 10W | N/A | No DS info
Test Stand | Valve |  | Received/Have | Yes | Fuel Vent Valve (solinoid) | 820 | 1 | $912.00 | Clark Cooper |  | 58 | Fuel Vent Valve (solinoid)
Test Stand | Valve Assembly |  | Not Spec'd |  | Main Fuel Valve |  | 1 |  | In house project |  | 68 | Main Fuel Valve - Electrically actuated Ball valve assembly
Test Stand | Valve Assembly |  | Not Spec'd |  | Main LOX valve |  | 1 |  | In house project |  | 69 | Main LOX Valve - Electrically actuated Ball valve assembly
Test Stand | Instrumentation |  | Received/Have |  | Flow meter |  | 1 |  |  |  | 70 | Flow meter
Test Stand | Instrumentation |  | Not Spec'd |  | LOX Flow meter |  | 1 |  |  |  | 71 | LOX flow meter
Misc items/ to be sorted
Type J Thermocouple | Engine | Thermocouple | Spec'd/Not Ordered |  | DH-1-24-J-12 | $21.00 | 2 | $42.00 | Omega | http://www.omega.com/pptst/BARE_SH_DH_OV_ELEMENTS.html | (Maybe 43) | What is up with this???? | 24 gauge, Double hole round insulated type J |  |  |  |  |  |  |  |  |  | max 1600C
Pressure Transducer | Engine | Pressure Transducer | Spec'd/Not Ordered |  | PX119-600GI | $99.00 | 1 | $99.00 | Omega | http://www.omega.com/pressure/pdf/PX119.pdf |  |  | Pressure transducer up to 600psi, 257 deg F and 20-500 Hz |  | DIN 43650C (mini DIN) |  |  | 4 - 20mA | 8 - 30VDC |  | 0 to 600psi |  | -40 to 135°C
A giant red button | Ignition System | Red Button | Spec'd/Not Ordered |  | Giant Red Button |  | 1 |  | Ryan |  |  | If not available, spec an old-timey dynamite plunger | Giant Red Button - Speak with Kristin | Telepathic | Brain Waves | Nightmares | Over 9000 | Over 9000 | Over 9000 |  | Over 9000 | Over 9000 | Over 9000 | Might as well scrap the project without this
 |  |  |  |  |  |  | Total: | $2973.13
 |  |  |  |  |  |  | Beta Funds: | $1000
 |  |  |  |  |  |  | Deficit | -$1973.13

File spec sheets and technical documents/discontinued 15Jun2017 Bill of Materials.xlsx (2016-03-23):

Part | Price | Quantity Purchased | Total Cost | Manufactuer / Distributor | Part # | Catalog Page # | Specifications Link
Frame
Wheel | $14.99 | 2 | $29.98 | Harbor Freight | 38943 | - | http://www.harborfreight.com/10-inch-pneumatic-rigid-caster-38943.html
Castor Wheel | $17.99 | 2 | $35.98 | Harbor Freight | 38944 | - | http://www.harborfreight.com/10-inch-pneumatic-swivel-caster-38944.html
Ground Screw | $13.97 | 4 | $55.88 | Home Depot | ANCFR16-ORG-A | - | http://www.libertyhardware.com/spiral-anchors-folding-ring/vortex-16-vortex-folding-ring-spiral-ancfr16-org-a.htm
Frame Material | $85.00 | 1 | $85.00 | Eastside Steel |  | N/A | N/A
Frame Material (2nd Purchase) | $17.00 | 1 | $17.00 | Eastside Steel |  | N/A | N/A
Blast Shield and Leg Material | $105.00 | 1 | $105.00 | Eastside Steel |  | N/A | N/A
Steel Round Bar | $5.41 | 6 | $32.46 | Lowes | 11620 | - | http://www.lowes.com/pd_44093-37672-11620___?productId=3057583&pl=1&Ntt=round+steel+bar
Aluminum Plate | $43.96 | 1 | $43.96 | Metal Supermarket |  | N/A | N/A
Total Cost |  |  | $405.26
Plumbing (Nitrogen)
Nitrogen Tank | $0.00 | 2 | $0.00 | Luxfer | L45J | - | https://docs.google.com/file/d/0By5gRimJqF9Nd0RONWxoN3dubW9hSHFnenJ0aWR2VzZTZ0lB/edit
7/8" to 1/2" compression fitting | $20.80 | 2 | $41.60 | Swagelok | SS-810-1-10ST | 17 | http://www.swagelok.com/downloads/WebCatalogs/EN/MS-01-140.pdf
1/2" to 1/4" tube adapter | $11.18 | 2 | $22.36 | Swagelok | SS-400-R-8 | 25 | http://www.swagelok.com/downloads/WebCatalogs/EN/MS-01-140.pdf
1/4" Branch Tee | $28.88 | 1 | $28.88 | Swagelok | SS-400-3-4TTM | 37 | https://www.swagelok.com/downloads/WebCatalogs/EN/MS-01-140.pdf
Needle Valve | $60.98 | 1 | $60.98 | Dixon / Amazon | MFS102 | - | https://www.dixonvalve.com/product/MFS102
Flexible Tubing | $32.70 | 1 | $32.70 | Associated Hose | 4R2AT-4'-204-B/E | N/A
Pipe Nitrogen | $2.57 | 12 | $30.84 | Swagelok | SS-T4-S-035-20 | 2 | http://www.swagelok.com/downloads/WebCatalogs/EN/MS-01-181.pdf
Ferrule Male Connectors | $7.35 | 5 | $36.75 | Swagelok | SS-400-1-4 | 13 | https://www.swagelok.com/downloads/WebCatalogs/EN/MS-01-140.pdf
1/4" Ferrule Tee | $23.40 | 2 | $46.80 | Swagelok | SS-400-3 | 35 | https://www.swagelok.com/downloads/WebCatalogs/EN/MS-01-140.pdf
1/4" NPT Hex Nipple | $6.32 | 4 | $25.28 | Swagelok | SS-4-HN | 4 | http://www.swagelok.com/downloads/WebCatalogs/EN/MS-01-147.pdf
1/4" NPT/ 1/4" Ferrule Elbow | $14.08 | 2 | $28.16 | Swagelok | SS-400-2-4 | 30 | https://www.swagelok.com/downloads/WebCatalogs/EN/MS-01-140.pdf
1/4" Female Tube Adapter | $10.15 | 4 | $40.60 | Swagelok | SS-4-TA-7-4 | 46 | https://www.swagelok.com/downloads/WebCatalogs/EN/MS-01-140.pdf
1/2" Female Tube Adapter | $13.77 | 2 | $27.54 | Swagelok | SS-4-TA-7-8 | 46 | https://www.swagelok.com/downloads/WebCatalogs/EN/MS-01-140.pdf
1/4" NPT Male Tube Adapter | $6.32 | 7 | $44.24 | Swagelok | SS-4-TA-1-4 | 43 | https://www.swagelok.com/downloads/WebCatalogs/EN/MS-01-140.pdf
1/4" Ferrule Cross | $42.54 | 1 | $42.54 | Swagelok | SS-400-4 | 40 | https://www.swagelok.com/downloads/WebCatalogs/EN/MS-01-140.pdf
Pressure Transducer (3000 psi) | $188.75 | 1 | $188.75 | Ashcroft / Grainger | G17M0215F23000 | - | http://www.ashcroft.com/datasheet_pdf/upload/datasheet-Transducers-G2.pdf
Ethanol Regulator | $523.86 | 1 | $523.86 | Swagelok | KCY1JRA412A20000 | 8 | http://www.swagelok.com/downloads/WebCatalogs/EN/MS-02-230.pdf
Oxygen Regulator | $523.86 | 1 | $523.86 | Swagelok | KCY1JRA412A20000 | 8 | http://www.swagelok.com/downloads/WebCatalogs/EN/MS-02-230.pdf
Check Valves | $48.55 | 2 | $97.10 | Swagelok | SS-4C4-1 | - | http://www.swagelok.com/downloads/WebCatalogs/EN/MS-01-176.pdf
Solenoids (Nitrogen) | $98.10 | 2 | $196.20 | Asco | 8262H080 | - | http://www.ascovalve.com/Applications/ProductSearch/ProductInfo.aspx?productid=8262H080AC120/60,110/50D&userAction=view&newView=yes
Manifold material | $62.00 | 1 | $62.00 | Alaskan Copper & Brass | 132132-3P | N/A | N/A
Relief Valves | $151.49 | 2 | $302.98 | Swagelok | SS-4R3A5-SETB | - | http://www.swagelok.com/downloads/WebCatalogs/EN/MS-01-141.pdf
Vent Valves | $131.08 | 2 | $262.16 | Asco | 8262H214 | - | http://www.ascovalve.com/Applications/ProductSearch/ProductInfo.aspx?productid=8262H214AC120/60,110/50D&userAction=view&newView=yes
Pressure Transducers (500 psi) | $188.75 | 2 | $377.50 | Ashcroft / Grainger | G17M0215F2500 | - | http://www.ashcroft.com/datasheet_pdf/upload/datasheet-Transducers-G2.pdf
Pressure Gauge (600 psi) | $19.44 | 2 | $38.88 | Winters / Amazon | PFP663ZRR1 | - | http://www.winters.com/PDF/PFP-ZR.pdf
Slic-Tite PTFE Thread Tape | $2.56 | 1 | $2.56 | La-Co / Amazon | 44094 | - | http://www.laco.com/assets/1/31/slic_tite_tape.pdf
1/4" NPT Cross | $74.55 | 1 | $74.55 | Parker / Grainger | 1/4 KMMOO-SS | F23 | http://www.parker.com/literature/Tube%20Fittings%20Division/Pipe_Fittings_&_Port_Adapters.pdf
Total Cost |  |  | $3159.67
Plumbing (LOX)
1/2" NPT Branch Tee | $46.48 | 1 | $46.48 | Swagelok | SS-810-3-8TTF? |  | https://www.swagelok.com/downloads/WebCatalogs/EN/MS-01-140.pdf
LOX Tank | $372.94 | 1 | $372.94 | Hoke / eBay | 8HD4G | 2 | http://catalog.hoke.com/Asset/79008ENG_Catalog.pdf
1/2" Ferrule Male Connectors | $16.98 | 5 | $84.90 | Swagelok | SS-810-1-8 | 13 | https://www.swagelok.com/downloads/WebCatalogs/EN/MS-01-140.pdf
3/4" Ferrule Male Connectors | $21.84 | 2 | $43.68 | Swagelok | SS-810-1-12 | 13 | https://www.swagelok.com/downloads/WebCatalogs/EN/MS-01-140.pdf
Cryogenic Ball Valve | $150.28 | 1 | $150.28 | Flowserve | C4466PMSE | - | http://www.flowserve.com/files/Files/Literature/ProductLiterature/FlowControl/WorcesterControls/WCEBR0013-02.pdf
1.5" NPT / 3/4" NPT Adapter | $15.42 | 2 | $30.84 | Merit Brass | 3614D-2412 | - | http://www.amazon.com/gp/product/B003LSSM1M?psc=1&redirect=true&ref_=oh_aui_detailpage_o04_s00
Bleed Valve | $50.82 | 1 | $50.82 | Swagelok | SS-BVM4 | 2 | http://www.swagelok.com/downloads/WebCatalogs/EN/MS-01-62.pdf
Pipe (LOX) | $0.00 | 0 | $0.00 | Swagelok | SS-T8-S-049-20 | 2 | http://www.swagelok.com/downloads/WebCatalogs/EN/MS-01-181.pdf
Total Cost |  |  | $779.94
Plumbing (Ethanol)
Pipe (Ethanol) | $0.00 | 0 | $0.00 | Swagelok | SS-T8-S-049-20 | 2 | http://www.swagelok.com/downloads/WebCatalogs/EN/MS-01-181.pdf
CGA 320 Nipple | $5.03 | 1 | $5.03 | Radnor | RAD64003970 | - | https://www.airgas.com/product/Gas-Equipment/Gas-Equipment-Accessories/Adapters-%26-Fittings/p/RAD64003970
CGA 320 Hex Nut | $3.67 | 1 | $3.67 | Radnor | RAD64003968 | - | https://www.airgas.com/product/Gas-Equipment/Gas-Equipment-Accessories/Adapters-%26-Fittings/p/RAD64003968
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

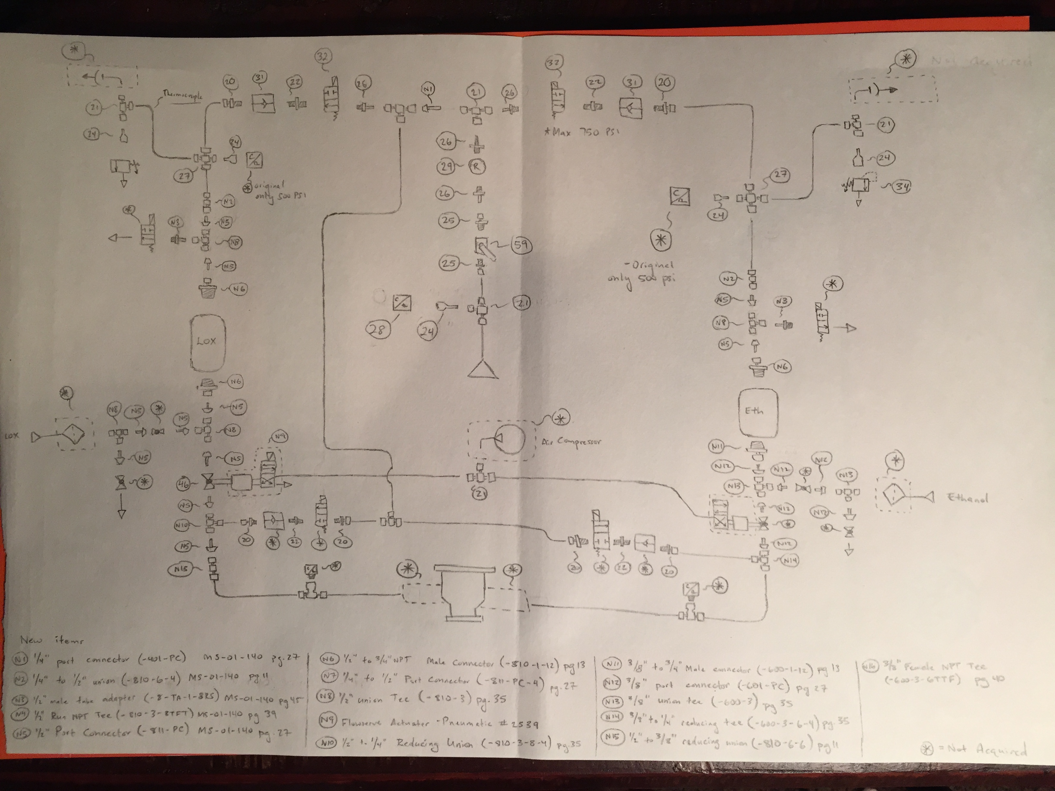
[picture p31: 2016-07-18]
BOM 160717.JPG

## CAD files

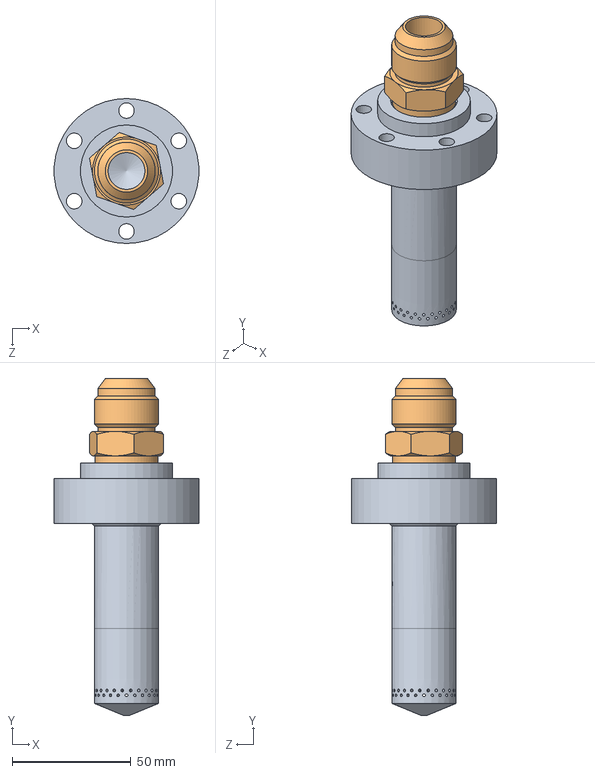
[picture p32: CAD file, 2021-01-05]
cad/Test Stand CAD Files/Version 2019-2020/engine_2020-05-21/pintleV7-5.SLDASM
60.8 x 141.8 x 61.0 mm
pintleV7-5
5482K126_PRECISION AN 37 DEGREE FLARED TUBE FITTING

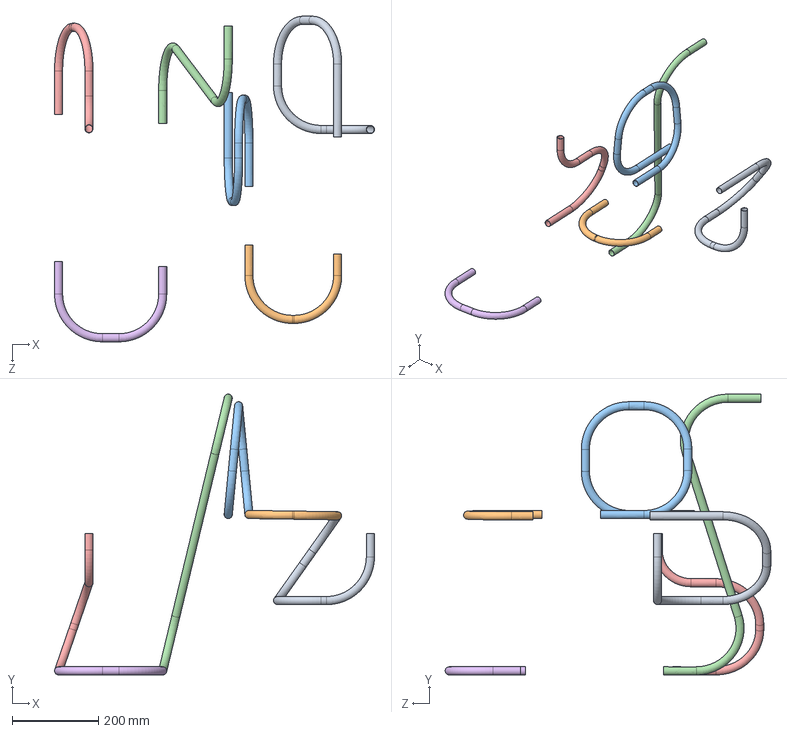
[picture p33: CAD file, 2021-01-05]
cad/Test Stand CAD Files/Version 2019-2020/Tube_5-Assembly_LFETS-001.sldasm
744.1 x 653.1 x 757.3 mm
Tube-750X028_4^Tube_5-Assembly_LFETS-001
Tube-750X028_17^Tube_5-Assembly_LFETS-001
Tube-750X028_11^Tube_5-Assembly_LFETS-001
Tube-750X028_18^Tube_5-Assembly_LFETS-001
Tube-750X028_16^Tube_5-Assembly_LFETS-001
Tube-750X028_10^Tube_5-Assembly_LFETS-001

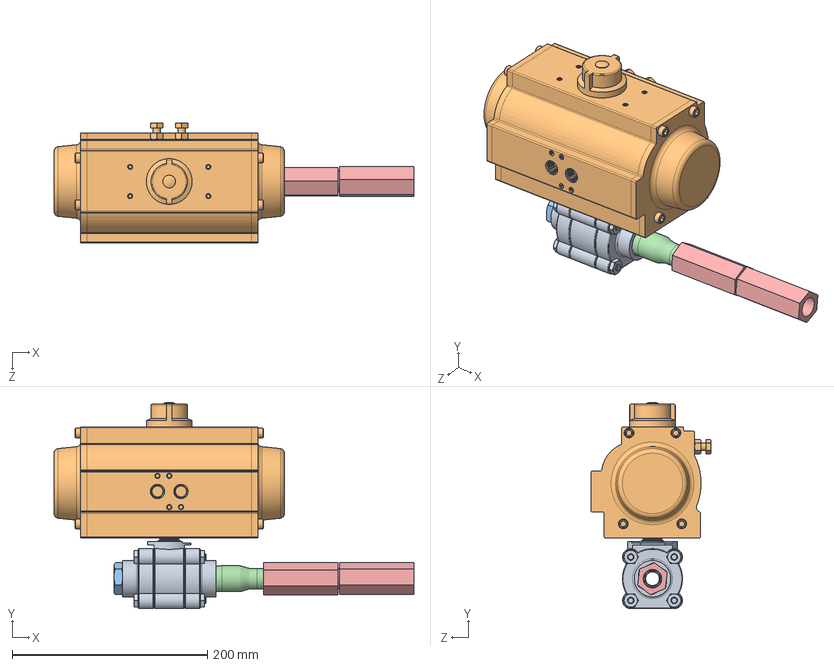
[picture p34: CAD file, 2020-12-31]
cad/Test Stand CAD Files/Version 2019-2020/Valves/SOV-1.SLDASM
368.6 x 211.4 x 122.9 mm
FAKE_sharpe_80BV
49935K880_AIR ACTUATOR FOR BALL-BUTTERFLY VALVE
51205K359_EXTREME-PRESSURE 316 SS THREADED PIPE FITTING
2161K140_THK-WALL SMOOTH-FLOW THRD REDUCE PIPE NIPPLE
Rego-CG500SS-check_valve x 2
4548K171_STANDARD-WALL 316316L SS PIPE NIPPLE

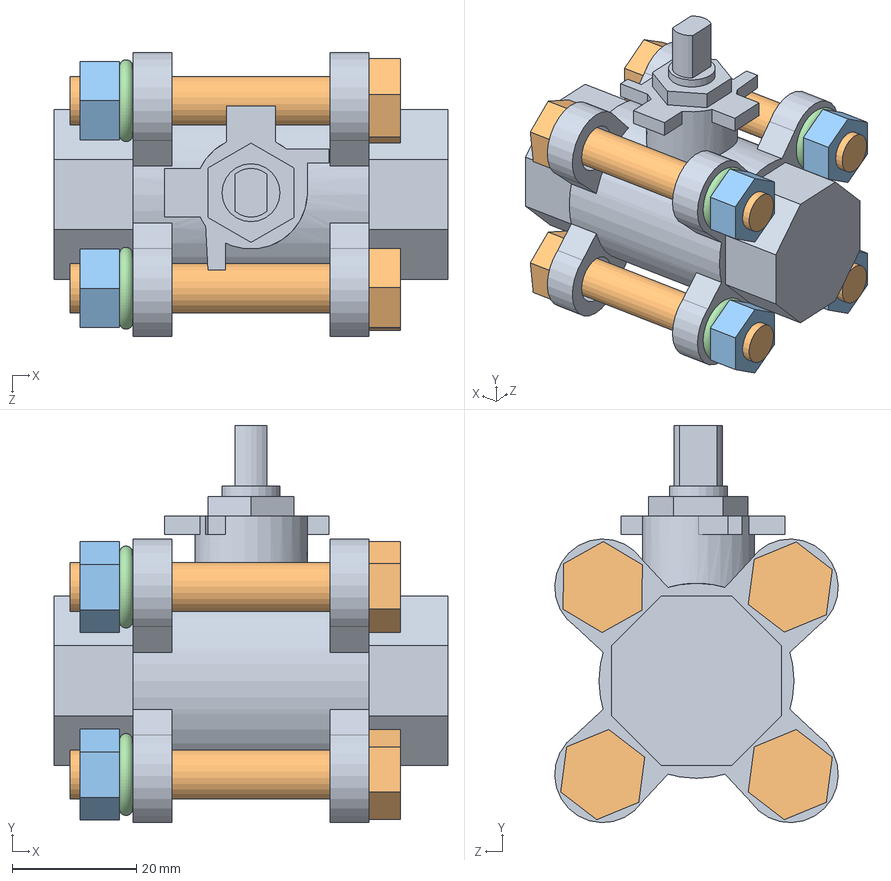
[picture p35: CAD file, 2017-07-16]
main propellant valves/Sharpe 39036 asm Valve Only.SLDASM
63.5 x 64.0 x 45.7 mm
Sharpe 39036
Sharpe 39036 Bolt x 4
Sharpe 39036 nut x 4
Sharpe 39036 washer x 4

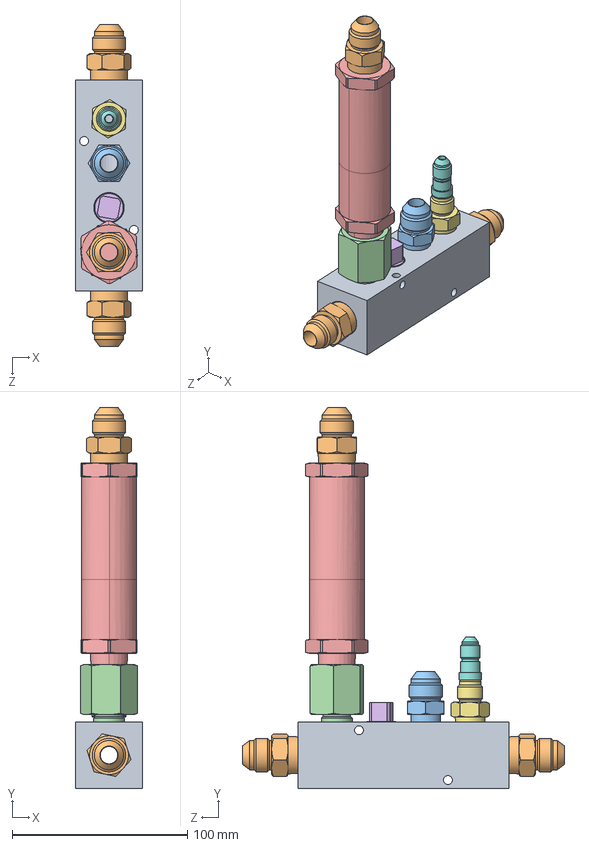
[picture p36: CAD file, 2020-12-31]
cad/Test Stand CAD Files/Version 2019-2020/LOX_N2_manifold_2.SLDASM
38.1 x 217.7 x 184.1 mm
6525N116_TYPE 316 STAINLESS STEEL MANIFOLD
50715K166_TYPE 316 SS 37 DEGREE FLARED TUBE FITTING x 3
50715K165_TYPE 316 SS 37 DEGREE FLARED TUBE FITTING
48805K460_PRECISION EXTREME-PRESSURE 316SS PIPE FITTING
HPRV-500_PSV-1,2
4443K713_HIGH-PRESSURE 316 SS THREADED PIPE FITTING
5482K122_PRECISION AN 37 DEGREE FLARED TUBE FITTING
5482K162_PRECISION AN 37 DEGREE FLARED TUBE FITTING

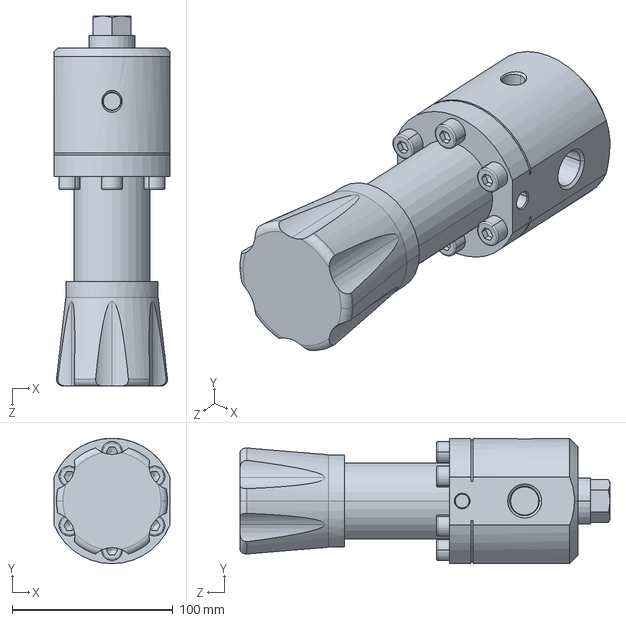
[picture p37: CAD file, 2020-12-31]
cad/Test Stand CAD Files/Version 2019-2020/Pressure_Regulators/PRV-1 & PRV-2 Assembly.SLDASM
72.0 x 78.0 x 230.1 mm

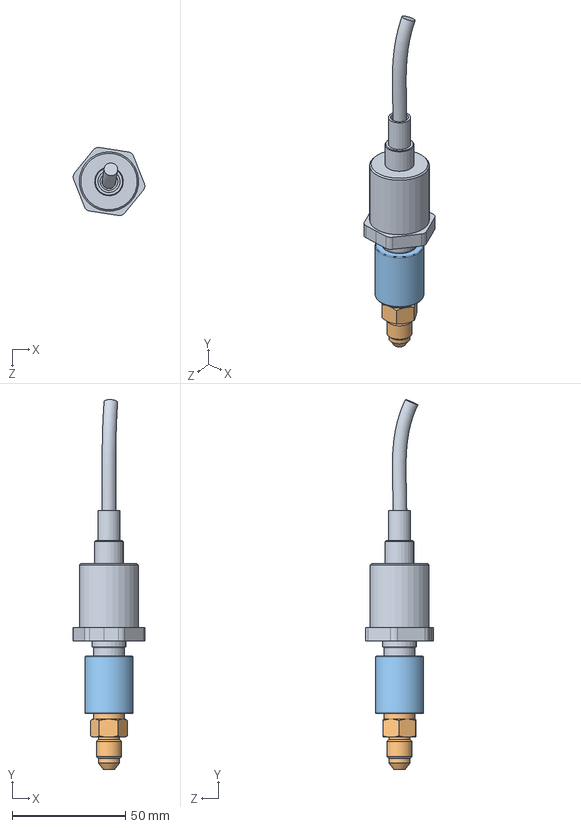
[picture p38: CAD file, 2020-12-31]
cad/Test Stand CAD Files/Version 2019-2020/Sensors/pressure_to_250_AN.sldasm
31.7 x 163.7 x 30.1 mm
Pressure_sensor_standin
5482K118_PRECISION AN 37 DEGREE FLARED TUBE FITTING
4452K112_TYPE 316 STAINLESS STL THREADED PIPE FITTING

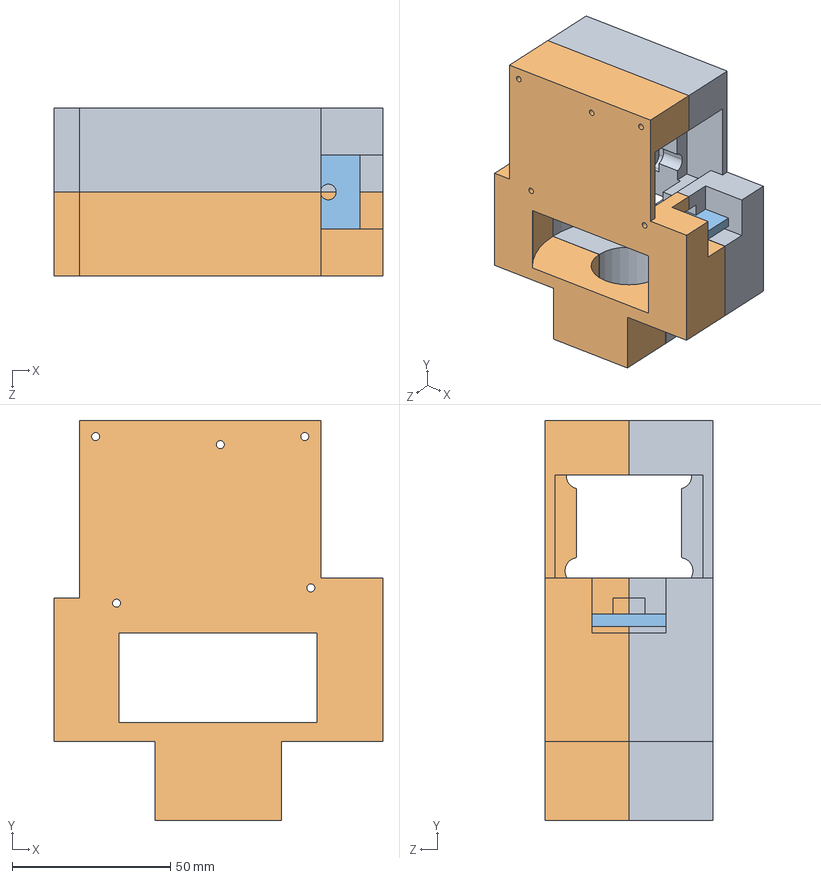
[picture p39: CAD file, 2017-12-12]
Main_Fuel_Valve/DC_Motor/cad/Housing_01.SLDASM
103.7 x 126.3 x 53.1 mm
Housing-Front
Housing-Back
LED_Head

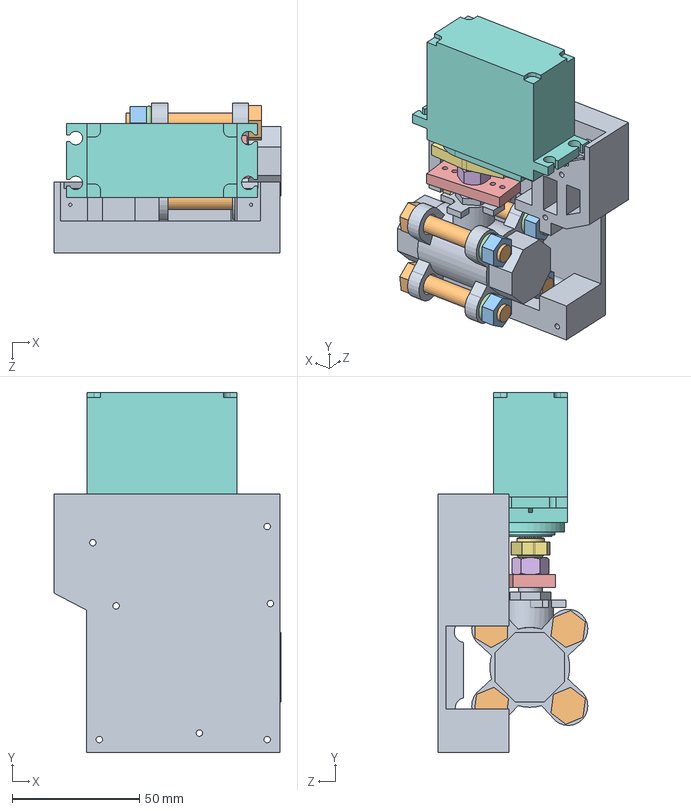
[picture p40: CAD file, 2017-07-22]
Main_Fuel_Valve/Servo_Motor/Sharpe 39036 asm.SLDASM
89.2 x 141.6 x 58.9 mm
Sharpe 39036
Sharpe 39036 Bolt x 4
Sharpe 39036 nut x 4
Sharpe 39036 washer x 4
Horn adapter
90473A210_LOW-STRENGTH STEEL HEX NUT
Servo Horn Mod
PowerHD 1235MG
Housing-Front 1.0

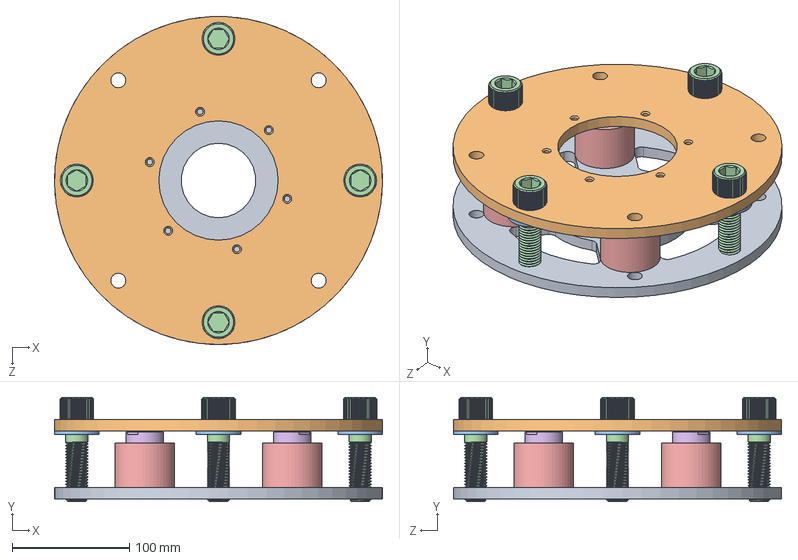
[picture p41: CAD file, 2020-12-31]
CAD/Test Stand CAD Files/Version 2019-2020/Load_Cell/load_cell_assembly.SLDASM
279.4 x 88.9 x 279.4 mm
load_cell_plate_R2_2020
load_cell_plate_mount_R2_2020
load_cell_bushing_2020 x 4
92196A846_18-8 STAINLESS STEEL SOCKET HEAD SCREW x 4
load_cell_2020_spacer_rebuild x 4
load_cell_FC23_dummy x 4
91292A033_TYPE 18-8 SS SOCKET HEAD CAP SCREW x 8

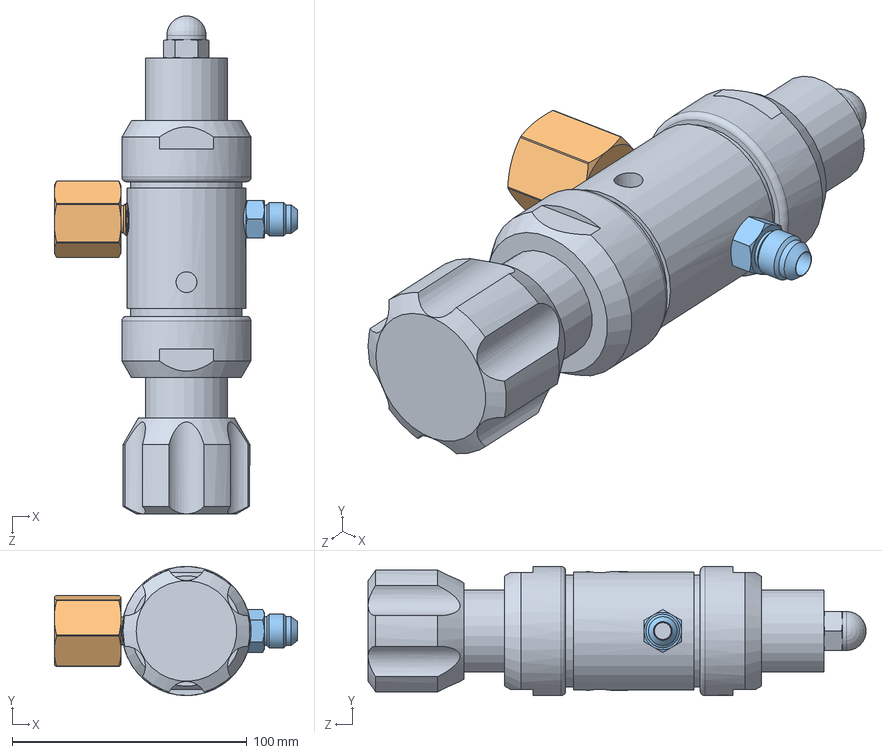
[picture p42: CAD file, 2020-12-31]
cad/Test Stand CAD Files/Version 2019-2020/Pressure_Regulators/PRV-3 Assembly.SLDASM
103.6 x 55.0 x 212.0 mm
KCY1JPA412A20000_PRT_29
51205K317_EXTREME-PRESSURE 316 SS THREADED PIPE FITTING
50715K163_TYPE 316 SS 37 DEGREE FLARED TUBE FITTING

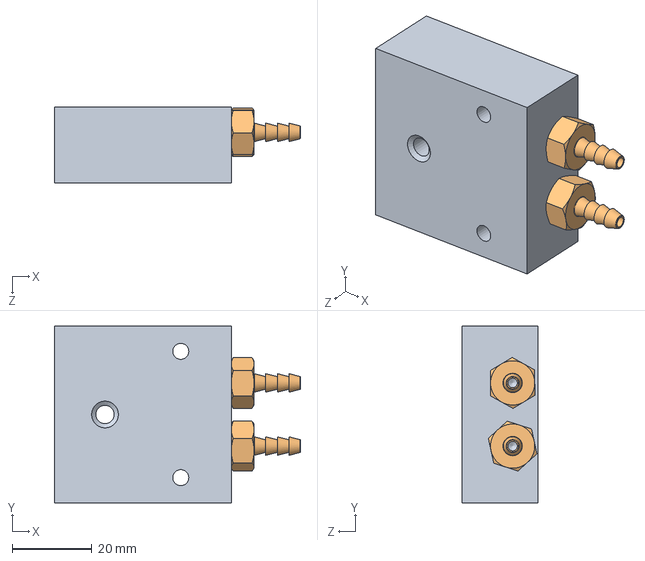
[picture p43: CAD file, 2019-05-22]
igniter/Igniter Mockup CAD/Torch Subassembly.SLDASM
61.8 x 44.5 x 19.1 mm
TorchBody
5346K610_BRASS BARBED HOSE FITTING x 2

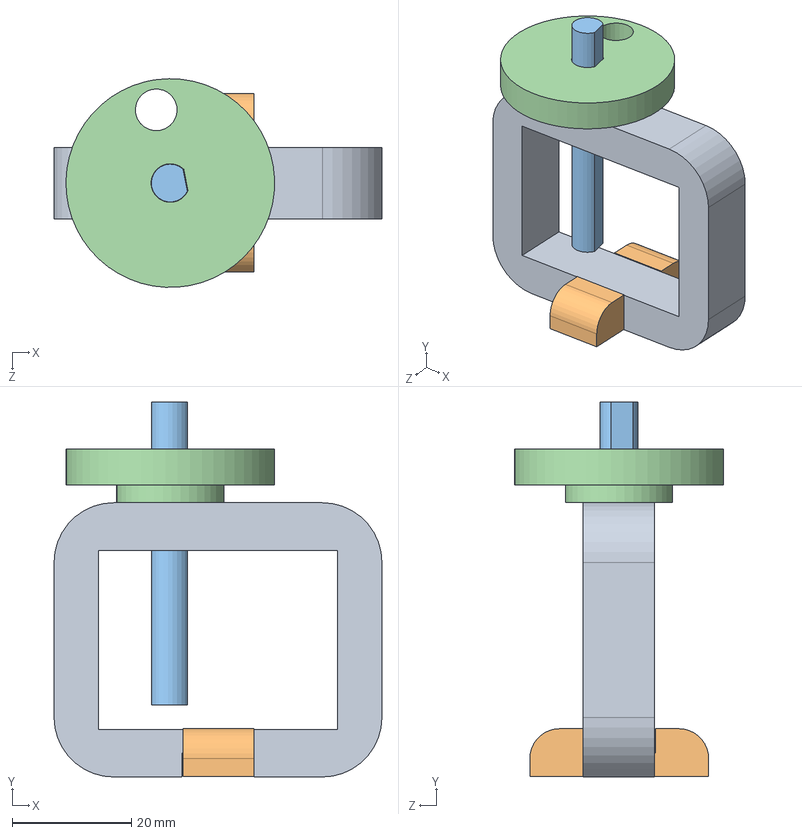
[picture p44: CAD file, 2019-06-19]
main propellant valves/MFV & LOX Actuator/Encoder Test Jig/Assem1.SLDASM
55.0 x 62.9 x 35.0 mm
Frame
Base
D-shaft-2in
knob

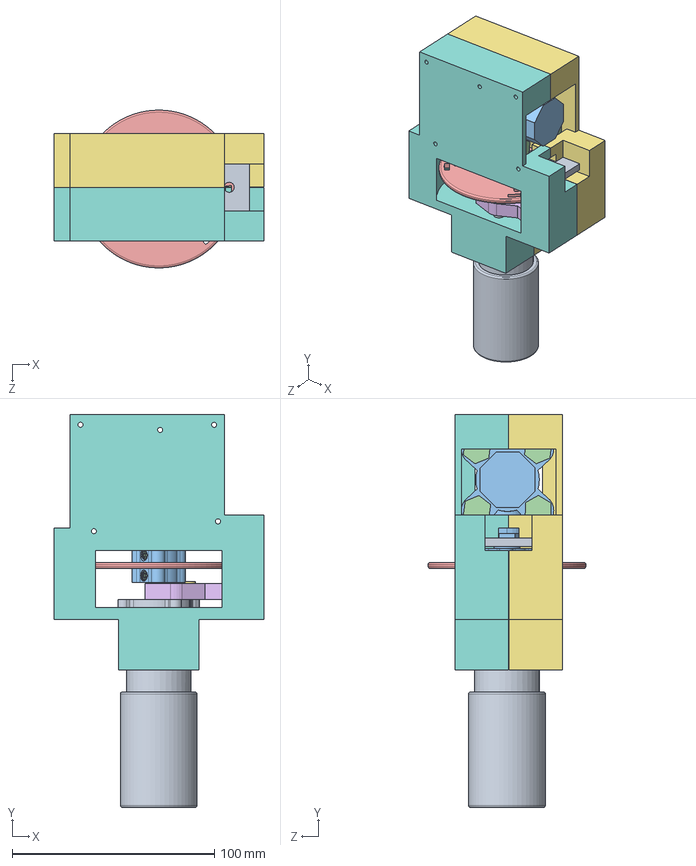
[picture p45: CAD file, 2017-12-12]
Main_Fuel_Valve/DC_Motor/cad/12VDC_valve_assembly.SLDASM
103.7 x 194.2 x 78.0 mm
555174_6-32_3mmx6mm_screw x 4
545576_10-32_set_screw x 2
encoding_wheel
Sensor_Head
Photo_sensor_5mm
Motor_12VDC_638263_shaft
Motor_12VDC_638263
92562A122_MIL SPEC ALLOY STEEL SOCKET HEAD CAP SCREW x 2
Sharpe 39036
Sharpe 39036 Bolt x 4
Sharpe 39036 nut x 4
Sharpe 39036 washer x 4
Housing-Front
LED_Head

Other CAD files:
cad/Test Stand CAD Files/2016/Tube_42-LMTS_5-001.sldasm
cad/Test Stand CAD Files/2016/Tube_38-LMTS_5.sldasm
cad/Test Stand CAD Files/Version 2019-2020/Tube_8-Assembly_LFETS-007.sldasm
cad/Test Stand CAD Files/2016/Tube_40-LMTS_5.sldasm
Archive/Torch-igniter/Igniter Mockup CAD/5346K610_BRASS BARBED HOSE FITTING.SLDPRT
Archive/Torch-igniter/Igniter Mockup CAD/FuelOxy Bottle.SLDPRT
Archive/Torch-igniter/Igniter Mockup CAD/Igniter Arm 1st Section.SLDPRT
Archive/Torch-igniter/Igniter Mockup CAD/Igniter Arm 2nd Section.SLDPRT
Archive/Torch-igniter/Igniter Mockup CAD/Igniter Hinge Plate.SLDPRT
Archive/Torch-igniter/Igniter Mockup CAD/Igniter Torch Attatchment Bracket Clamp.SLDPRT
Archive/Torch-igniter/Igniter Mockup CAD/Igniter Torch Attatchment Bracket.SLDPRT
Archive/Torch-igniter/Igniter Mockup CAD/Igniter Torch.SLDPRT
Archive/Torch-igniter/Igniter Mockup CAD/Main Assembly.SLDASM
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

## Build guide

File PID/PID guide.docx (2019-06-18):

# PID guide

# Updates to previous version

## Removal of N2 manifold

Previous setup for the nitrogen gas tank for pressurizing the system was replaced with a quick disconnect, and the nitrogen gas tank will be considered as separate from the test stand. It will be a separate N2 tank that will be connected to the test stand using flexible tubing to the quick disconnect.

## Valves

Valves for upper fuel and LOX sections specified for designated required system pressures.

## Removal of igniter system

Igniter system was removed due to difficulties in machining the engine given to us. It is now a separate external system from the test stand. It is now replaced with three way fittings with caps in case of future integration of an internal igniter.

## Venturi meters

The venturi meters were moved to before the main fuel and LOX valve due to the need for room for the required entry length for the flow to fully develop.

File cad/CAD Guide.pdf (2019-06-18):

# Liquid Fuel Engine Test Stand CAD Beginners Guide and Revisions

Last Updated: 5/30/2019
Authors: Matthew Ng
Contact: matther_ng@yahoo.com

General Information | 3
Updates from previous version | 3
Re-designing of the test stand | 3
Swagelok fittings to AN 37o fittings | 3
Material change from brass fittings | 3
Igniter System Changes | 4
Elimination of fittings | 4
Addition of joggles to tubes | 4
Updated placeholders | 5
Pressure panel placement | 5
Updated test stand structure | 5
Updated load cell engine mounting | 5
Place Holders | 5
- Fuel vent valve | 5
Tubing Guide | 5
- General Guidelines | 5
- Tubing Process | 6
- Drawings for Manufacturing | 12
- CAD Fitting resources | 13

# General Information

All necessary Solidworks files can be found at https://github.com/psas/liquid-engine-test-stand/tree/master/cad/SW_CAD
Note: Most components aside from fittings were created using dimensions from calipers and are only accurate for dimensioning purposes.

# Updates from previous version

Introduction

As with designing any product having a good idea of what components are needed and where they go are essential. While evaluating the computer generated model left by the previous capstone team it was clear that it did not accurately reflect what was planned as some components were not up to date and some were missing. As shown in Fig 13 the test stand was heavily re-designed to better represent what was going to be constructed.

Swagelok fittings to AN 37o
fittings
Most of the fittings for both the fuel and LOX side have been switched from swagelok to AN 37o fittings. This is because AN fittings perform well under vibration, high pressures, and cryogenic conditions. The sleeve used to back up the flared end of the tube ensures tube alignment with fitting axis, reduces mechanical strain on tube, and compensates for vibrations. The flared end has a minimal change in geometry compared to swagelok resulting in negligible pressure losses. The threads for AN fittings are coarser which provides individual threads with more strength and resists cross-threading, a common issue with the fine-threaded swagelok fittings.

Material change from brass fittings
The original design called for a mixture of stainless steel, brass, and aluminum fittings. Under the redesign the stand now has three distinct sections, each with its own material selections. The pressure panel is built out of swagelok brass fittings and aluminum tube. Aluminum tube was used as brass fittings were available and seal well with aluminum. The fuel side of the stand, below the fuel tank, will consist of aluminum materials only except for valves. Currently it is a mixture of brass and aluminum. The oxidizer side is made from stainless steel. This will allow for better maintenance of the system as each section can be pulled apart for storage reducing corrosion. Stainless steel was used for the liquid oxygen transport as it works well at cryogenic temperatures and is not significantly reactive with oxygen. Eventually brass and aluminum should be eliminated from the system. Aluminum is extremely subject to attack by corrosion and brass becomes brittle as galvanic corrosion pulls zinc from the alloy.

Igniter System Changes
The engine provided did not have enough supporting material around the pre-existing igniter port for one to be installed. Instead, to simplify machining and avoid the issue, an external ignition system was devised. The next iterations of the engine will rely on advances in printing technology or on post-processing to provide a tap for the igniter.
The new design of the test stand gives the option for use of an external igniter, via a spring-loaded armature. This arm is designed to be able to hold an external ignition source in the correct position, until engine ignition, at which point the arm will be “blown” away from the engine. If the 2.2kN engine is tested on the stand, this armature will provide the ignition source, and it gives engine designers of future iterations of the engine an option of using an internal or external ignition source.

Elimination of fittings
The stand had been designed with fittings wherever tubing needed to change direction. Fittings give the tubing a discontinuous internal surface and create very large losses on direction changes. To reduce pressure requirements tube bending replaced most of the fittings. Bent tube has near-negligible pressure loss and are more robust with geometry changes due to high pressure or extreme temperature.

Addition of joggles to tubes
Since pipes have a high coefficient of thermal expansion, cryogenic temperatures will cause the tubes to contract which can result in leaks at fittings where pre-load is lost. Adding joggles to long sections of tube relieve this by allowing the tubes extra length to straighten out instead of losing pre-load.

Updated placeholders
New models have been integrated into the CAD to better represent the dimensions of the components that will be installed. These models include new LOX valves for size and flared fittings, main LOX valve for actual dimensions, and main fuel valve for actual dimensions. Most models are rough volume estimates purely for dimensioning.

Pressure panel placement
The pressure panel section has been moved behind the firewall to better protect it from unscheduled engine structure integrity checks. This also allows for a modular firewall to be installed on the front of the stand without need for pressure panel mounting.

Updated test stand structure
The previous CAD did not match the test stand “as built” due to warpage from welding and other imperfections in fabrication. The CAD was updated to match the physical stand. Hold-down plates and other precision components including the teflon tank cushions were designed using the updated dimensions.

Updated load cell engine mounting
The thrust-plate model from a 2017 master’s thesis was imported into the design.

# Place Holders

## - Fuel vent valve

EH40-08 normally closed valve CAD added for general dimensioning.

# Tubing Guide

## - General Guidelines

Depending on what you are looking for pipes are measure by inner diameter and tubes are measured by outer diameter. Tubing dimensions were used for this version of the CAD so all references to tube diameter will refer to an outer diameter.

## - Tubing Process

1. If connecting AN 37

o
fitting import part | titled “Flared pipe end” with the
corresponding tube diameter you are looking for. If connecting Swagelok fitting move on to step 2
2. Create a new part in the assembly | and click anywhere in the work area to
confirm
3. Right click the newly created part found in your parts list and click on edit part

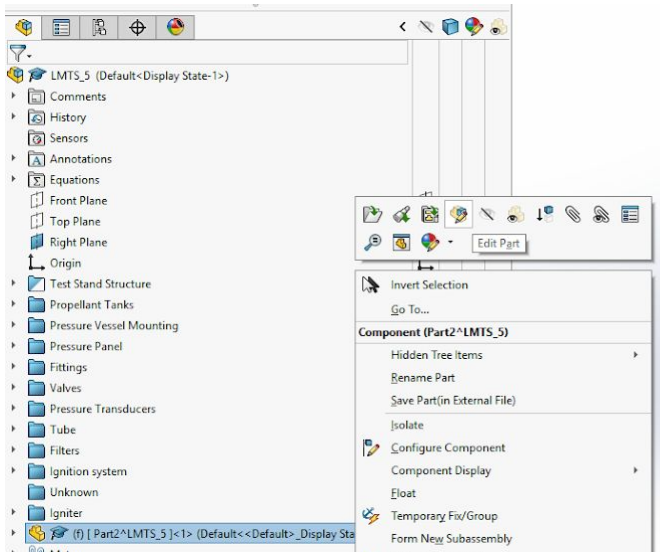
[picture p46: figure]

4. Go to the sketch tool and create a 3D sketch

5 Using the line tool sketch your path from fitting to fitting from the face of the flared pipe end

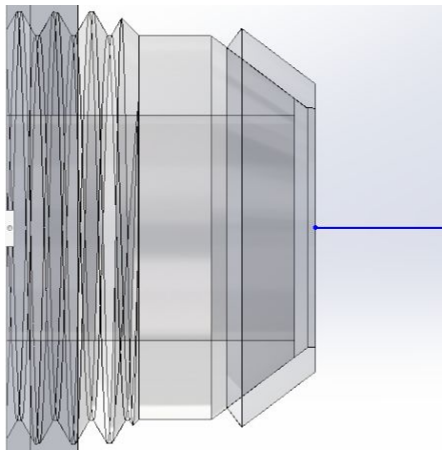
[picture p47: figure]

or to the back face of the Swagelok fitting.

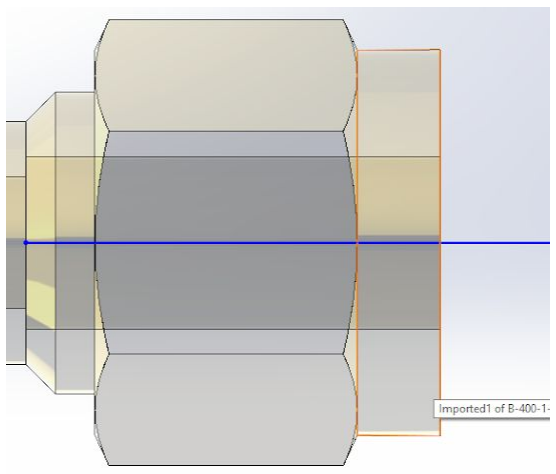
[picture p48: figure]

Note: To make room for fittings and bending during construction all initial and ending lengths of tubing must be 1.5 inch or more. Additionally to help center and make sure the faces are touching you can mate the end point of the line to the fitting using the coincident and concentric mate. This can be done by holding down ctrl and selecting the end point and any circular feature.

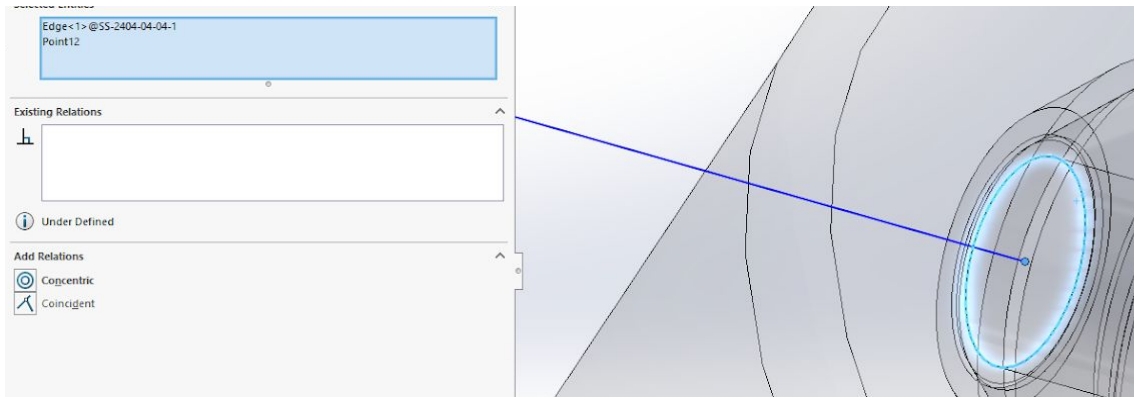
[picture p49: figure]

However, make sure to delete those relations after you are done as they can affect any rebuilds to the tube.

6. To add bends use the sketch fillet tool by clicking on the desired corner
Note: Follow minimum bend radius according to the rocket bible found in the PSAS rocket room. In this version of the CAD .25 inch tube uses 7/8th inch bend radius and .5 inch tube uses 2 inch radius.
7. For long lengths of straight pipe include a joggle if possible

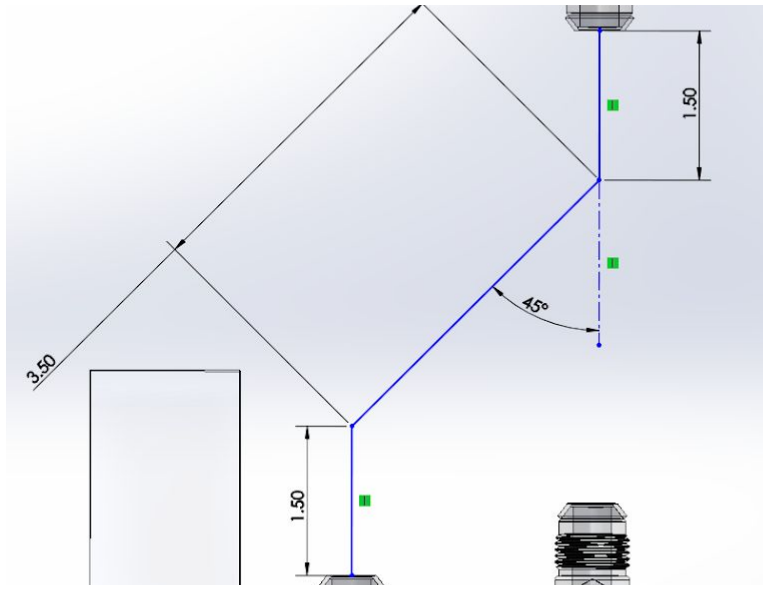
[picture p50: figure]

Note: Due to manufacturing constraints the middle length of any joggle must be 3.5 inches or more. This version of the CAD uses an 45

o offset for the joggle. The angle can be adjusted for anything below 90

o however it has not been tested how that affects the minimum middle length for manufacturing. All joggles in this version of the CAD use a 45

o offset purely for uniformity.

8. Exit the sketch and go to insert -> weldments -> structural member

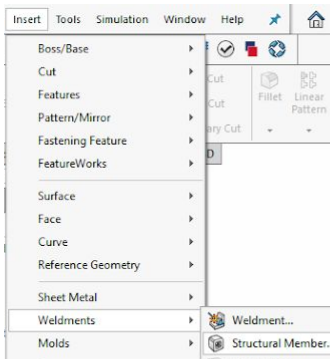
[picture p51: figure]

Click on the beginning section of your sketch and then the following section until you have selected all then press enter

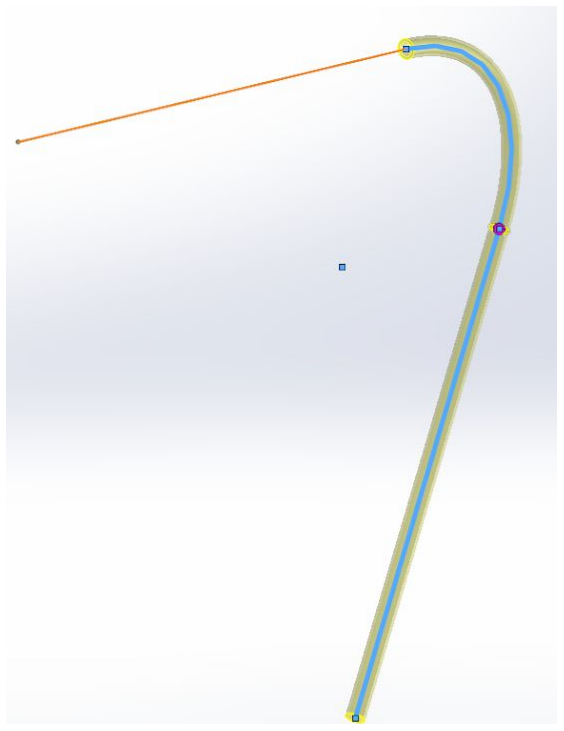
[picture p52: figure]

9. Left click on the pipe feature found under the part in the parts list, right click on the sketch feature then click on edit sketch.

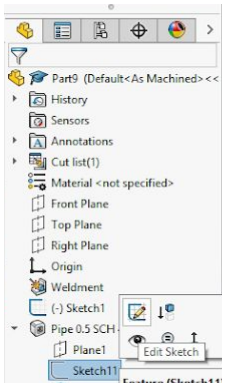
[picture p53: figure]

Delete the construction line leaving the outer and inner diameter. Edit the dimensions for the inner and outer diameters according to what you desire.

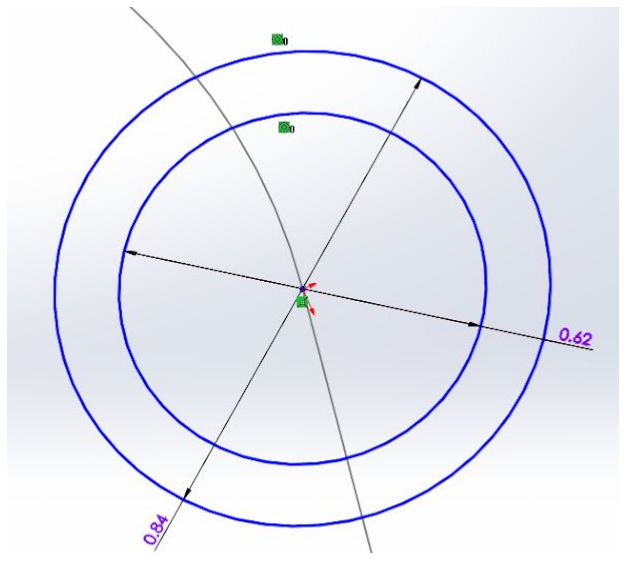
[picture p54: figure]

Note: This version of the CAD .5 inch tube has an inner diameter of .416 inches and .25 inch tube has an inner diameter of .206 inches. These values are based off the minimum wall thicknesses found in the rocket bible according to 3,000 psi (much larger psi than what will actually be operating at)

10. Right click on the part found in the parts list and click save part (in external file)

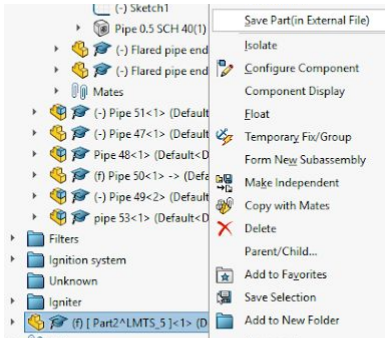
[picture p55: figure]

Note: To reuse any tube designs import another one into the assembly, right click on it and click make independent. Make sure to make the tube part independent as making assemblies independent will not make the tube part independent which can result in other tubes change when you are editing one if another assembly has the same tube part.

11. If flared pipe ends are used make a new assembly | and drag the tube part
and its corresponding flared pipe ends into the new assembly.

## - Drawings for Manufacturing

Tube dimensions:
Diameter
Center to center (from endpoint of one length to the beginning point of the next length) Straight lengths (from endpoint to end of flared end if used)

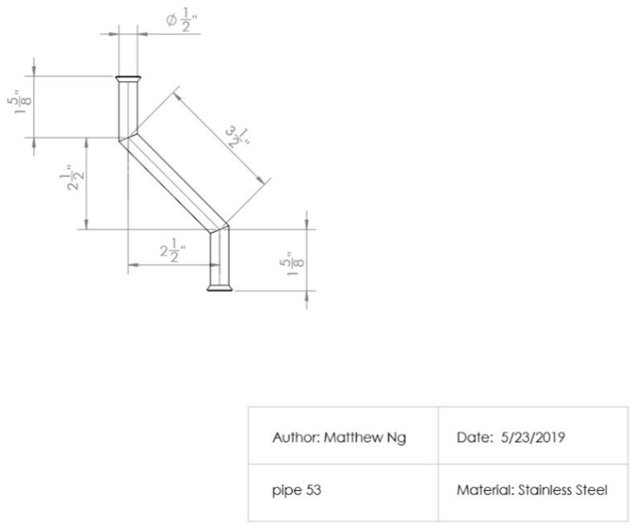
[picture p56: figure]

Format: In 1/8ths can be done by going to system properties then document properties -> Units -> Fractions

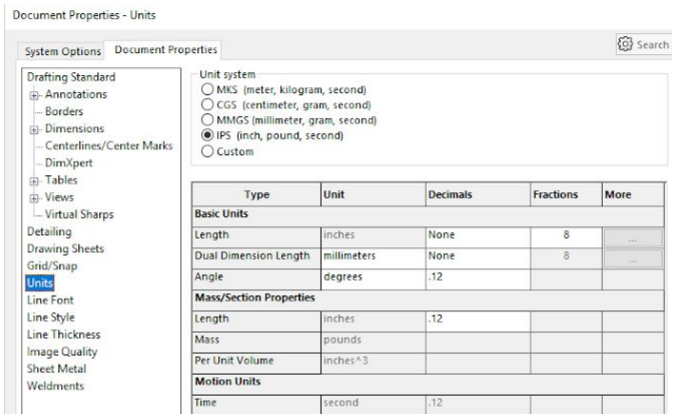
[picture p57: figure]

More examples can be found on Github in the CAD section under pipe orders https://github.com/psas/liquid-engine-test-stand/tree/master/cad/SW_CAD/Pipe%20orders

Note: Convert drawings into PDFs as Solidworks drawings require the solidworks part file to open.

## - CAD Fitting resources

More information on fittings can be found in LFETS -> LFETS and LFE Technical -> Component Documentation -> Piping Hardware
https://brennaninc.com/
https://www.mcmaster.com/
https://www.swagelok.com/en

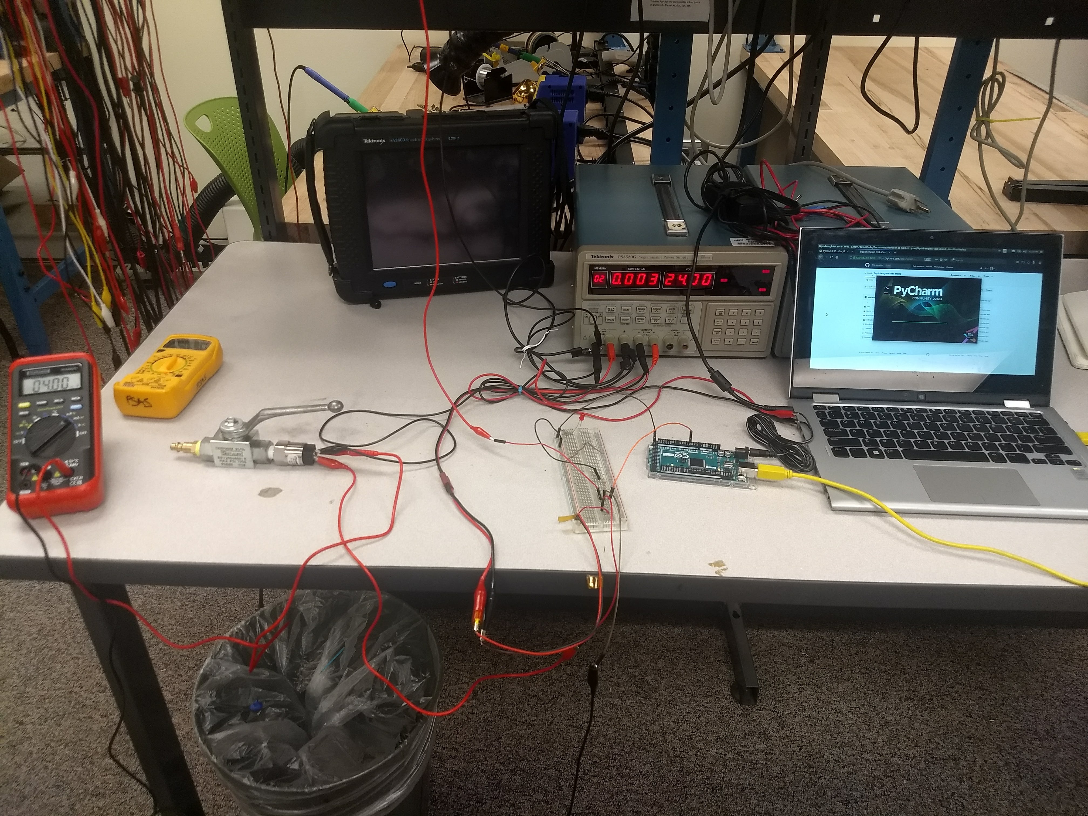
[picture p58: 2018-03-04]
TSAR/ArduinoCode/PressureTransducer/images/setup.jpg

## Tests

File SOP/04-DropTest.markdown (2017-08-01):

---
title: Drop Tower Test
layout: base
---

# Drop Test Procedures

## Common Setup
Start with the Avionics Stack on the rocket cart and batteries charged.

 1. Verify that there are no spurious cables attached, and all flight cables are in place except for Battery and Dev Umbilical
    - All cables should have Retaining Nuts attached
    - Cable lengths should be secured to the Avionics Frame as if for flight
 1. Attach the Dev Umbilical Cable
 1. Attach the Flight Battery Cable and related Retaining Nuts
 1. Verify RNH powers up (green blinking LED)
 1. Attach Shorepower
 1. If doing a full droptest proceed to section Droptest, else proceed to section Pretest

### Pretest (baseline)
 1. Verify section Common Setup has been followed
 1. After RNH powers up use fc-test to power on all ports.
    - See Rocket Cart Procedures
 1. After FC boots ssh to the FC as root
 1. Git pull the FCF repo
 1. Build the FCF for flight
 1. Clean the log directory
 1. **Critical section start**
 1. Start the FCF code
 1. Verify FCF is logging and telemetry is streaming to the telemetry viewer
 1. Detach shorepower and remove the Dev Umbilical Cable
 1. Wait for some time
 1. Gently wiggle the cart as a time marker
 1. Wait for some time
 1. Reattach the Dev Umbilical Cable
 1. ssh into the FC
 1. Stop the FCF
 1. Copy log file to laptop, check into Launch-11/droptest, push to github
 1. **Critical section end**
 1. Proceed to section Common Shutdown

### Droptest
 1. Verify section Common Setup has been followed
 1. Set up as much drop tower as possible, so we can drop as soon as FC stack is running
 1. Remove FC from cart and place in drop test enclosure
 1. Place test rig in drop tower
 1. Use fc-test to power on all ports
 1. After FC boots ssh to the FC as root
 1. git pull the FCF repo
 1. Build the FCF for flight
 1. Clean the log directory
 1. **Critical section start**
 1. Start the FCF code
 1. Verify FCF is logging and telemetry is streaming to the telemetry viewer
 1. Remove the dev umbilical cable and shorepower
 1. Follow droptower procedures for countdown, drop, and recovery
 1. Reattach the dev umbilical cable
 1. ssh into the FC
 1. Stop the FCF
 1. Copy log file to laptop, commit into Launch-11/droptest, push to github
 1. **Critical section end**
 1. Proceed to section Common Shutdown

## Common Shutdown
 1. Reattach shorepower
 1. Remove from droptower
 1. Shutdown the FC
 1. Power down all ports
 1. Disconnect the battery

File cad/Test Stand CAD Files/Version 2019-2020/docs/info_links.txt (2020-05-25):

how to create tubing drawings:
https://seacadtech.com/define-routing-spool-segment/

flange allowances:
https://www.hoseandfittingsetc.com/technical-info/jic-tube-end-assembly

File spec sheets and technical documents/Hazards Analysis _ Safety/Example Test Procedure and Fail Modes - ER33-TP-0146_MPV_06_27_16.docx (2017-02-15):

ER33-TP-0146

Revision-Baseline

EFFECTIVE DATE: 6/27/2016

George C. Marshall Space Flight Center

Marshall Space Flight Center, Alabama 35812

Fast-Aero Multiport Valve (MPV) Test

Engineering Directorate

Propulsion Systems Department

Propulsion Component Design and Development Division

Valves, Actuators, and Ducts Design & Development Branch

ER33

Component Development Area

DOCUMENT HISTORY LOG

Status (Baseline/ Revision/ Canceled) | Document Revision | Effective Date | Description
Baseline | - | 6/27/2016

APPROVALS

Gustavo A. Martinez 6/27/2016

ER33 Document Originator Date

ER33 CDA Lead Date

ER33 Team Lead Date

QD12 Industrial Safety Date

ER33 Test Personnel Date

TABLE OF CONTENTS

# 1. scope

This procedure defines the test requirements to test the Fast-Aero Multiport Valve (MPV). The primary objective is to investigate flow Characteristics, distribution, and leakage of the valve using LN2. This valve uses parts manufactured using SLM and this test will exercise those parts under pressure in water and in LN2.

# 2. purpose

The purpose of this test procedure is to ensure that the Fast-Aero Multiport Valve (MPV) is tested in a safe and controlled way. All testing shall be performed at the Component Development Area (CDA) located at Building 4656.

# 3. Test description

Testing of the valve will be under separate pressurized and flow rate test conditions. The MPV will start out at 100% closed whiles LN2 is flowed to flood the downstream side of the MPV to chill in the flow line. HOV-1 and … will remain open during chill in. A series of tests will occur with the valve being cycled from fully-closed-to-fully-open-to-fully-closed under pneumatic actuation by a Series CVQ Pneumatic Actuator. Another series will occur under various dP’s and flow rates with the valve being cycled from fully-closed to fully-open under pneumatic actuation.

Testing of the MPV valve assembly is to take place in different sequences:

1. The valve will be hydrostatically proof tested per the standard CDA procedures. The valve will have successfully completed proof testing, and the test results will be on file prior to beginning this test. Pretest internal and external leak checks will also be performed. The valve will be leak checked to confirm build and actuator setup. This test will be performed using the standard CDA procedures and is not part of this procedure. The test will be conducted using 25 to 50 psig GN2 with the valve commanded closed. The valve will be checked for external leakage using soap solution, and internal leakage using a bubble-o-meter. Leakage in excess of zero bubbles per minute shall be dispositioned by the test requestor and/or test engineer prior to proceeding with subsequent tests.
2. Pretest baseline stroke will be performed. With zero pressure on the valve and the valve pneumatically actuated. The valve will be cycled from fully-closed-to-fully-open-to-fully-closed; a minimum of 3 times while recording data. This test is performed to verify valve health and actuator function prior to water and LN2 flow testing.
3. During initial chill in of the valve, internal leakage will be checked using bubble-o-meter, or low flow flowmeter. Also, with the valve chilled against the upstream side, an LN2 internal leak check will be made at 50 +/-25 psig prior to and after final test runs. The MPV will be commanded fully-closed for internal leak checks. Internal leakage testing will occur with the MPV outlet ports capped off or the tube end fittings plugged.
4. For the water flow test, the upstream side of the MPV will be flooded with the MPV valve held closed and the tank regulated to a pressure of 50 to 100 psig and then the MPV opened to flow water through the outlet ports and data recorded.
5. For the LN2 testing, LN2 will be flooded to the upstream side of the MPV to chill in the inlet line up to the valve whiles the MPV is held closed. During the first chill in 50 to 100 psig pressure will be generated upstream down and through the bleed valve—HOV 1.
6. With the MPV fully-closed and LN2 at various inlet pressures, the MPV will be taken to the gauge pressure defined in the test request. Once the target pressure has been established, the MPV will be cycled between full-closed-to-full-open-to-full-closed at a rate and duration defined in the test request. Maximum MPV inlet test pressure for this sequence will be 1500 psig. Actuator pneumatic pressure range for this test will be 50 to 100 psig. Sequence 3 will be repeated after flow testing in sequence 6.

Table 1 – Pressure Drop Test Conditions

Inlet Pressure (psig) +/-10% | Outlet Pressure (psig) +/- 10% | Estimated Full Open Flowrate (GPM)
50
100
250
500
750
1000
1500

Density LN2 = 50.38 lb/ft^3 Density Water = 62.4lb/ft^3

# 4. reference documents

96M19158 CDA Fluid Schematic

MWI 1700.2C System Safety Program

MPR 1840.2C MSFC Hazard Communication Program

MPR 8730.5 Control of Inspection, Measuring, and Test Equipment

MWI 8710.1 “Inspection and Certification Process for Pressure Vessels and Systems (PVS)”

MPR 8715.1 Marshall Safety, Health, and Environmental (SHE) Program

MWI 8715.15E Ground Operations Safety Assessment Program

MPR 8823.2 Pressure Systems Guidelines and Certification Requirements

ANSI 13.1 Schemes for the Identification of Piping Systems

ASME B31.1 Power Piping Code

ER33-PLAN-CDA Component Development Area Operation Plan

Test Requirements MFV Full Flow Test Requirements

# 5. safety precautions

The Test Article MPV valve is customer supplied and has been proofed to 3000 psig and documentation provided by the customer. This test will occur via the North West Bunker using the 500 gallon run tank system at CDA. This test is not designed to test component structural integrity. All personnel operating CDA fluid systems shall be certified for those operations per MWI 341~0.1.

Use extreme caution when conducting pneumatics and/or venting operations during tests. Use approved personal protective equipment (PPE):

A. Eyes: Safety glasses shall be worn when venting or purging systems.
B. Ears: Earplugs or earmuffs shall be used where excessive noise levels occur near filling and venting operations.
C. Hands: When handling test fixtures, protective gloves shall be worn.

Do not remove a test unit from a pressurized line. Test set-up provides vent valve to bleed pressure from the test article. Verify that the test article is vented prior to removal.

Only personnel certified to work on high pressure systems are allowed access to the test area while facility systems are pressurized. Personnel may only enter the test area with permission by the Test Engineer. All personnel shall wear approved personal protective equipment for the operation being performed as defined below:

General Operations:

Eyes | Safety glasses with side shields shall be worn during fabrication of metallic components such as tubing and panels. Visiting personnel shall wear safety glasses.
Feet | Closed-toe shoes that cover the top of the foot or boots with trouser legs extended over the top of the boot shall be worn during operations. Safety shoes shall be worn while performing lifting operations or if in areas where lifting operations are being performed.
Body | Cuff-less long trousers worn outside boots or over shoes shall be worn.
Ears | Each occupant shall carry earplugs or earmuffs. Venting operations inside the CDA or in other areas within the building occur with very short notice.
Head | A hard hat shall be worn if lifting operations are being performed in the high bay.

Cryogenic & Pressurized Systems (> 150 psig):

Eyes | Safety glasses with side shields shall be worn. Visiting personnel shall wear safety glasses with side shields. Full Face Shields shall be worn when transferring cryogen.
Hands | Gloves shall be worn to prevent injury to hands from cryogenic burns. Clean leather gloves shall be worn if more protection is needed.
Feet | Closed-toe shoes that cover the top of the foot or boots with trouser legs extended over the top of the boot shall be worn.
Body | Long-sleeved clothing, cuff-less long trousers worn outside boots or over shoes shall be worn.
Ears | Earplugs or earmuffs shall be used when venting gases.

If any personnel injury occurs, the following is offered as a guide:

- Isolate or remove the hazard from the area.
- Move injured personnel only if necessary to prevent further injury.
- Call for medical help.
  - Medical/Ambulance 911
  - Fire Department 911
  - Security 544-4357
  - Environmental Incident 911
  - Utilities 544-3919
  - Blood Cleanup 544-4000
  - Medical Center 544-2390
  - Safety Hotline 544-0046

# 6. test hardware description

This section defines the test hardware to be used during the tests.

## 6.1 Mechanical Systems

6.1.1 The flow system used for this test series will utilize the 500 gallon tank system at 4656 with LN2 flow media. The run tank has 500 gallon capacity, 2900 psig capability. RV-119, set to protect the test article, is set at 2750 psig and all testing will use 1500 psig maximum supply pressure. Valves are manipulated either manually prior to pressurized system or pneumatically for those requiring manipulation while the system is pressurized.

6.1.2 The test article MPV valve is a pneumatically actuated linear position valve designed for cryogenic propellant. It has a stroke of ~2.4 inches. The valve body is manufactured from additively manufactured Inco 718 while several of its internal parts are either commercial or traditionally machined parts. The MPV has one (2-inch) inlet and 48-outlet ports.

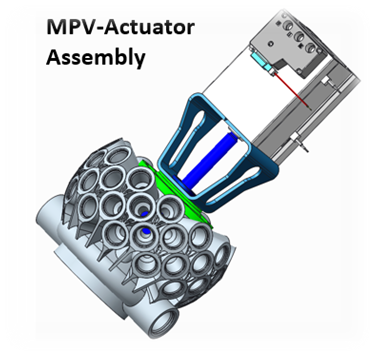
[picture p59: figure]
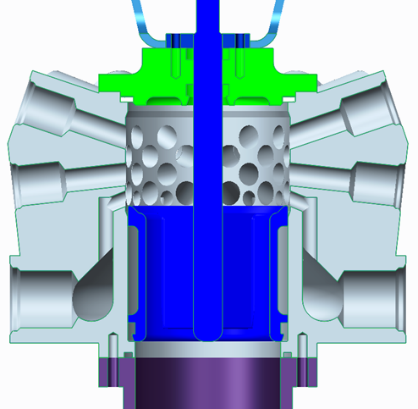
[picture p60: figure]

## Test Article MPV and Actuator

## 6.1.3 Instrumentation

    6.1.4 PWG Systems’ TopCAT2008 is a general-purpose data acquisition hardware and software package designed to control the National Instruments TM SCXI Data Acquisition Hardware. This software is designed to operate and control SCXI Chassis modules connected to an E or M Series Data Acquisition Cards or an SCXI-1600 Data Acquisition Module. Modules include: SCXI-1520 (8-Channel ¼, ½, Full Bridge Strain Gage Module), SCXI-1102 (32- Channel TC Input Module (2-Hz BW), SCXI-1160 16-Channel SPDT Relays.
    6.1.5 All data acquisition and control will be provided by a National Instruments SCXI Chassis and LabView® software running a computer. During the tests, the data acquisition and control equipment as well as the Test Conductor will be located in Room 103 of the Component Development Area (Building 4656). A 24 VDC power supply will provide power to the SOVs and excitation power to the pressure transducers. A 9 VDC power supply will provide power to the relay

Figure 1a. Test Set-up

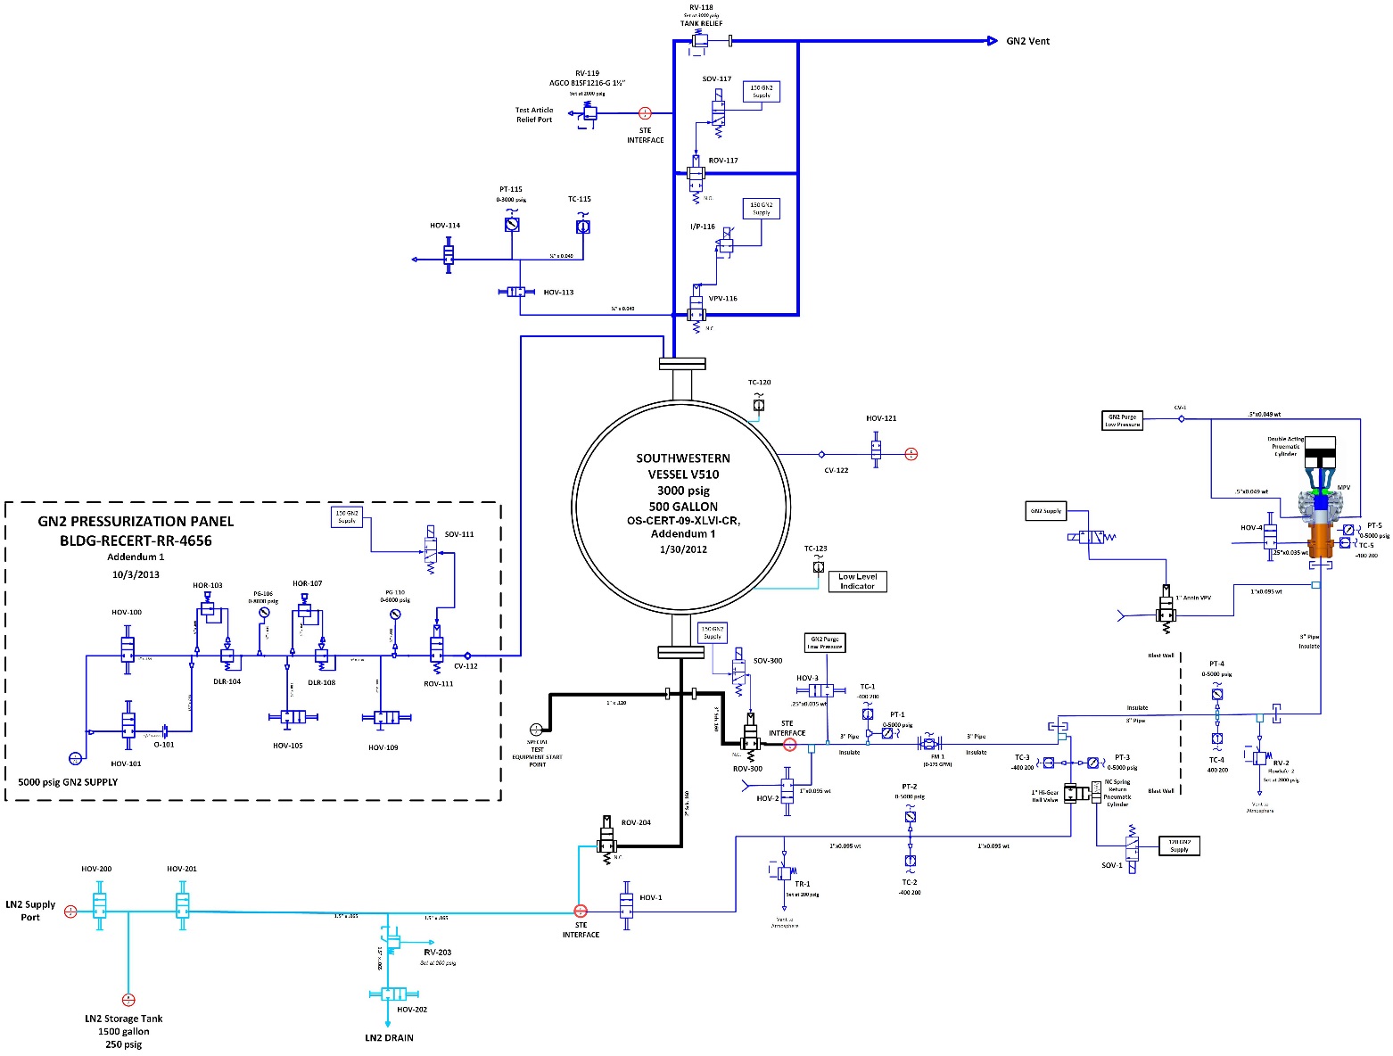
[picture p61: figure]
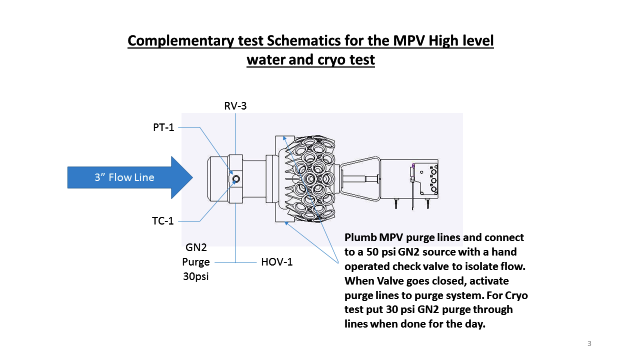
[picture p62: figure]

Figure 2 GN2 Distribution Panel

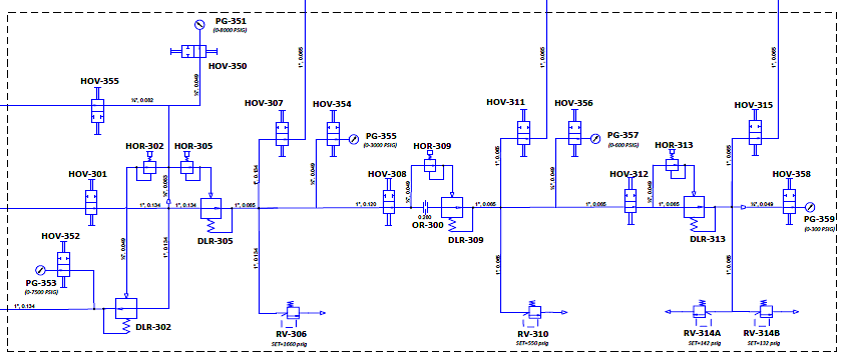
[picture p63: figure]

Figure 3 Liquid Nitrogen Storage System

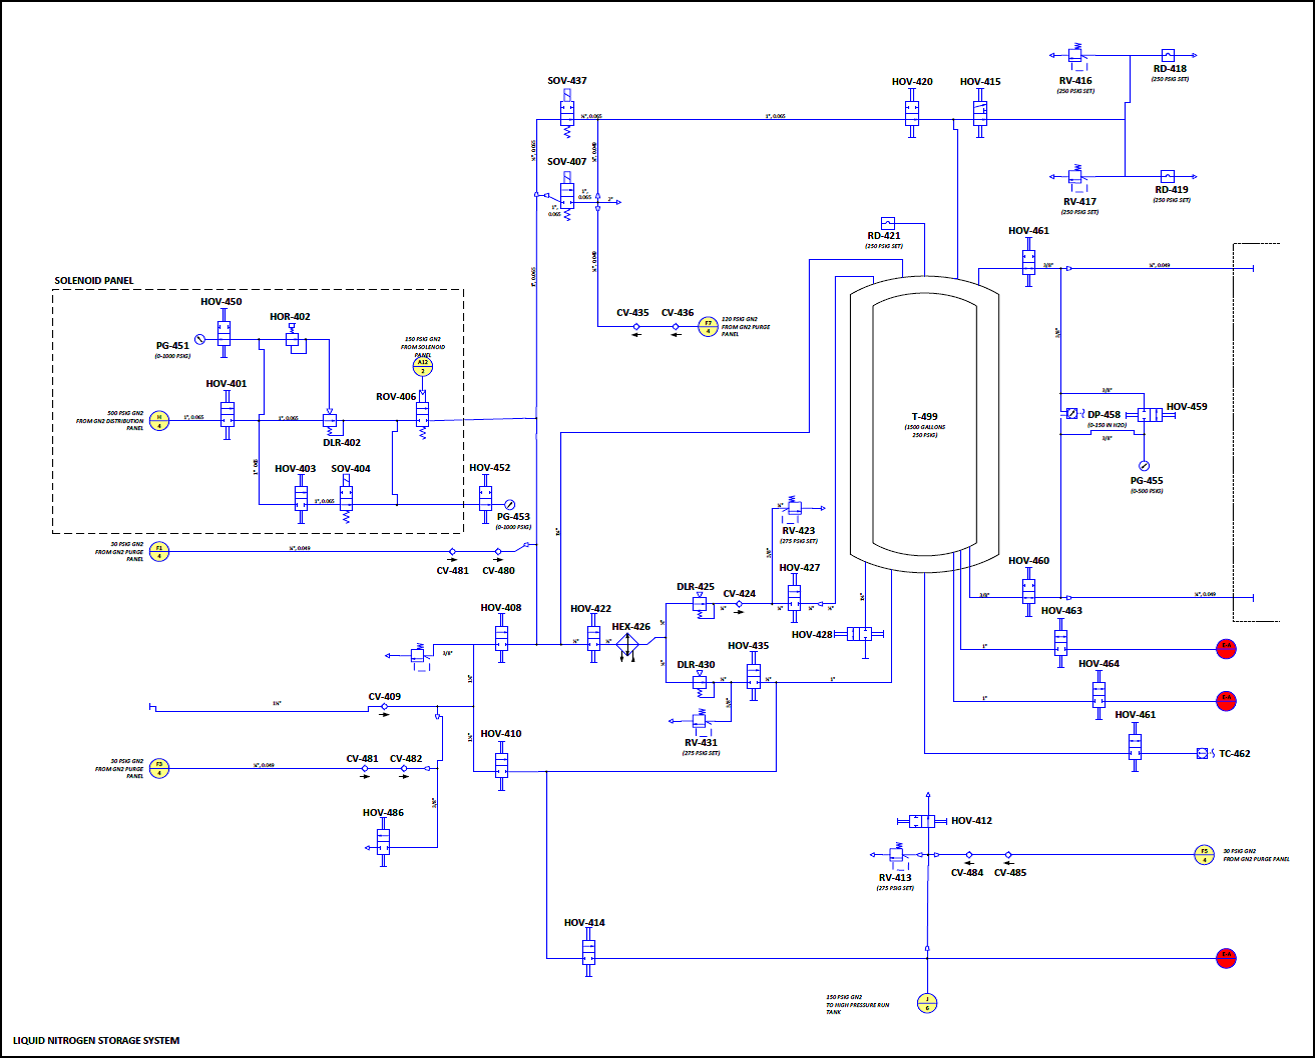
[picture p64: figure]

# 7.0 initial test set-up

This section defines the steps to establish the initial conditions for the LN2 system.

The zero state conditions for the LN2 and GN2 systems are shown in the 3 below.

Table 3: Test System Zero State Conditions

Component ID | Description | State
HOV-100 | High Flow Isolation valve | Closed
HOV-101 | Low Flow Isolation Valve | Closed
HOR-103 | First Stage Hand Regulator | Closed
DLR-104 | First Stage Dome Loader | Closed
HOR-107 | Second Stage Hand Regulator | Closed
DLR-108 | Second Stage Dome Loader | Closed
HOV-105 | First Stage Isolation Valve | Closed
HOV-109 | Second Stage Isolation Valve | Closed
ROV-111 | Main GN2 Isolation Valve | Closed
HOV-113 | Instrumentation Bleed Valve | Closed
HOV-114 | Instrumentation Bleed Valve | Closed
VPV-116 | GN2 Vent Valve | Closed
ROV-117 | GN2 Vent Valve | Open
HOV-121 | 150 PSIG GN2 Purge Isolation Valve | Open
HOV-200 | Fill Isolation Valve 1 | Closed
HOV-201 | Fill Isolation Valve 2 | Closed
HOV-202 | Vent/Drain Valve | Open
VPV-204 | Main Tank Isolation Valve | Closed
ROV-300 | Main Test Article Isolation Valve | Closed
ROV-400 | Alternate Test Article Isolation Valve | Closed
MPV | Test Article Valve | Closed
HOV-1 | Flow Meter Bypass Valve | Closed
HOV-2 | Run Line Drain Valve | Closed
HOV-3 | Run Line Purge Valve | Closed
HOV-4 | MPV Bleed Valve | Closed
HOV-6 | MPV Purge Valve | Closed
ROV-5 | Flow Meter Bypass Line Isolation Valve | Closed
VPV-1 | MPV Vent Valve | Closed

Component Nominal Conditions

# 7.1 initial test set-up

Step Number | Description | Verification | Notes
7.1.1 | Verify test personnel are trained and certified to operate/maintain cryogenic systems.
7.1.2 | Lock or Barricade All Access Points to the Test Control Area
7.1.3 | Walk Down the System and Verify Proper Initial State all Components. Verify no relief valves are mounted such that personnel are affected by discharge.
7.1.4 | Notify All Test Personnel the Potential for Loud Venting Exists. Test Personnel shall utilize appropriate PPE.
7.1.5 | Verify Emergency stop functionality
7.1.6 | Verify that live feed camera is operational | | Camera is set up for live video feed and recording of testing
7.1.7 | Clear All Non-Essential Test Personnel from the Control Area. All Access Will Be Controlled through the Test Control Room

# 7.2 Initial GN2 Purge (~30 psi GN2 purge)

Step Number | Description | Verification | Notes
7.2.1 | Actuate MPV to 100% Open
7.2.2 | Verify ROV-300 is closed. Verify ROV-204 is closed. | | Isolate test article and LN2 feed lines
7.2.3 | Open VPV-1
7.2.4 | Open ROV-5, HOV-1, HOV-202 | | Purging test article and LN2 feed lines
7.2.5 | Open HOV-3 | | Start Purge
7.2.6 | When lines purged, Close HOV-202, HOV-1, ROV-5 | | Traps GN2 in LN2 feed line and FM bypass line
7.2.7 | Close HOV-3 | | Stops test article feed line purge
7.2.8 | Open HOV-4 and HOV-6 | | Initiates purge through test article’s purge valve

# 8. LN2 Tank Procedures

This section defines the steps to establish fill and chill procedures for the LN2 run tank and draining the tank at the conclusion of the test.

# 8.1 sEQUENCE 4 Ln2 RUN tank Fill Procedures

Step Number | Description | Verification | Notes
8.1.1 | Verify Test leg in purge state (7.2.1-7.2.8)
8.1.2 | Close ROV-300, Close ROV-111, Close HOV-1 | | Isolate the tank supply
8.1.3 | Open HOV-113 to Expose PT-115/TC-115 to tank environment
8.1.4 | Verify HOV-114 is Closed
8.1.3 | Regulate HOR-103/HOR-107 on DLR-104/108 to 0 Psig | | Zero out supply pressure
8.1.4 | Open HOV-414 , Open HOV-412 to chill transfer line | | Chill transfer line.
8.1.5 | Close HOV-412 when transfer line chilled | | Ready tank fill
| This space intentional | | This space intentional
8.1.6 | Verify Close ROV-111, Verify Close ROV-300, Verify Close VPV-204 Verify Close HOV-201
8.1.7 | Open VPV-116 to vent tank, then Open ROV-117 | | (CAUTION: LOUD VENTING!) Loud Venting if tank pressurized- Tank Vents to ambient
8.1.8 | Close VPV-116
8.1.9 | Verify/ Prepare Dewar For LN2 transfer 8.1.2 – 8.1.5
8.1.10 | Open HOV-201, Open VPV-204 | | Initiates tank filling
8.1.11 | Continue Fill run tank to full
8.1.12 | To refill or top off, repeat 8.1.6 – 8.1.12

# 9. TEST RUNS

This section defines the test runs to be performed.

# 9.1 Sequence 5 Testing – Internal Leak Check

Step Number | Description | Verification | Notes
9.1.1 | Verify ROV-300, ROV-204, ROV-111, and HOV-1 are Closed. Verify ROV-117 and VPV-116 is Open, and tank is full | | Tank is Full
9.1.2 | Adjust HOR-103/HOR-107 on DLR-104/DLR-108 to provide 0 psig supply pressure read on PG-110 | | Upstream ROV-111 at 0 psig
9.1.3 | Verify PT-1,PT-2, are at 0 psig
9.1.4 | Verify the MPV Test Article set to proper run position | | Fully Closed - Refer Test Request
9.1.5 | Hook up Tygon tubing to HOV-4 outlet and route to bubble meter or flowmeter | | Leak flow hook up
9.1.6 | Verify No Personnel Inside Bunker | | Clear all persons from inside bunker
9.1.7 | Open HOV-4 | | Bleed valve Open
9.1.8 | Close VPV-1 | | Isolates test leg outlet
9.1.9 | Open ROV-5
9.1.10 | Open HOV-1 | | Allow flow of LN2 under tank head through flow meter bypass
9.1.11 | Open HOV-201
9.1.12 | Begin Recording Data
9.1.13 | Witness leakage through bubble meter as chill in occurs up to MPV inlet | | Chill in up to MPV inlet
9.1.14 | Monitor TC-1, TC-3, and TC-4 to ensure LN2 reaches upstream of ROV-300 | | Control VPV-1 if needed
9.1.15 | Close ROV-5 when liquid TC-1 reads LN2 temperature
9.1.16 | Open ROV-300, Open ROV-204 | | Chill run line
9.1.17 | Ensure run line and tank are full
9.1.18 | Close ROV-204 when LN2 is seen at VPV-1 outlet | | Isolate LN2 dewar
9.1.19 | Open HOV-202 | | Drains the bypass and dewar fill line
9.1.20 | Verify PT-2 is reading 0 psig and note temperature of TC-2 | | Line is drained
9.1.21 | Close HOV-1
9.1.22 | Close HOV-202

# 9.2. Sequence 6 Testing – Cryo (LN2) flow TEST

Step Number | Description | Verification | Notes
9.2.1 | Verify No Personnel next to Test Article or Inside Bunker | | Clear all persons from inside bunker and around Test Article
9.2.2 | Close VPV-1
9.2.3 | Verify Test Article set to proper initial run position | | Refer Test Request, 100% Closed
9.2.4 | Close ROV-117 and VPV-116 | | Ready to pressurize
9.2.5 | Verify 0 psig on PG-110 and PT-115
9.2.6 | Open ROv-111
9.2.7 | Adjust HOR-103/DLR-104 and HOR-107/DLR-108 to provide test pressure per test request
9.2.8 | Verify pressure per test request on PT-115/PT-1/PT-5
9.2.9 | Begin Recording Data
9.2.10 | Cycle the MPV from 100% to 100% Open at the slew rate requested | | BEGIN RUN
9.2.11 | Close the test article | | END RUN
9.2.12 | Stop Recording Data
9.2.13 | Adjust HOR-103/DLR-104 and HOR-107/DLR-108 to provide next test pressure per test request
9.2.14 | Repeat ____ - ____
9.2.15 | If Tank needs filling proceed to ____
9.2.16 | Close ROV-111
9.2.17 | Adjust HOR/103/DL-104 and HOR-107-DLR-108 to provide 0 psig
9.2.18 | Verify 0 psig using PG-110
9.2.19 | Open VPV-116 to vent tank
9.2.20 | Verify 0 psig using PT-115/PT-1/PT-4/PT-5 | | Vented system
9.2.21 | Proceed to Section 8.1 LN2 Tank Fill Procedures | | Adjust VPV-1 as needed
| End of Testing | | End of Testing

# 10. ln2 run tank vent and drain operations

# 10.1 LN2 RUN TANK VENT AND DRAIN OPERATIONS

Step Number | Description | Verification | Notes
10.1.1 | Close HOV-100 to isolate the GN2 Pressurization System. | | Remove system pressure
10.1.2 | Close ROV-111 to isolate the GN2 Pressurization System | | Isolate tank supply
10.1.3 | Slowly Open VPV-116 to Vent LN2 Tank to 0 psig (CAUTION: LOUD VENTING!) Then Open ROV-117 | | (CAUTION: LOUD VENTING!)
10.1.4 | Regulate HOR-103/HOR-107 on DLR-104/DLR-108 to 0 psig as read on PG-106/PG-110
10.1.5 | Verify 0 psig on PT-115/PT-1/PT-5
10.1.6 | Actuate the MPV to 100% Open
10.1.7 | Close ROV-300
10.1.8 | Open HOV-2 | | Drain System
10.1.9 | Open HOV-3 | | Start run line purge
10.1.10 | Open HOV-4 | | Start MPV purge

# 11. emergency operations

This section defines operations to be undertaken should an emergency arise during testing.

## A. Emergency Phone Numbers

  - Medical/Ambulance 911
  - Fire Department 911
  - Security 911
  - Environmental Incident 911
  - Utilities 544-3919
  - Medical Center 544-2390
  - MSFC Safety Office 544-0046

## B. Personnel Injury

If a personnel injury occurs during the execution of this procedure, the Test Conductor must determine whether the injured person is currently safe from test facility hazards so that medical attention may be sought immediately, or if facility systems need to first be shut down to ensure safety. Regardless, immediately call 911 so that medical assistance can be on their way. If facility systems need to be shut down first, before attending to the injured person, then execute Section 11.1.1-11.1.4 before continuing with this section.

## 1. ( ) Call 911 for medical assistance.

## 2. ( ) Isolate or remove the hazard from near the injured person if appropriate to prevent additional injuries.

## 3. ( ) Do not move the injured person unless it is necessary to prevent further injury.

## C. Loss of Electrical Power

## If a loss of electrical power occurs during the execution of this experiment, the system will go to safe state with vents going open. Electrical power is re-established; the Test Conductor will assess where to resume execution of the test procedure.

## D. Emergency Shutdown

Refer to Section 7 of ER33-PLAN-CDA, “Component Development Area Operation Plan” for locations of emergency gas shutoffs.

# 11.1 emergency operations for test article Anomoly Shutdown

Step Number | Description | Verification | Notes
11.1.1 | Close ROV-111 to isolate tank from GN2 Pressurization
11.1.2 | Open VPV-116 to remove pressure from Water Run Tank, then Open ROV-117 (LOUD VENTING) | | (CAUTION: LOUD VENTING!)
11.1.3 | Close ROV-300 to isolate test article from water/LN2 Run Tank

# 11.2 emergency operations for Loss of Power

Step Number | Description | Verification | Notes
11.2.1 | ROV-111 will fail Closed to isolate the Run Tank from the Pressurization Source
11.2.2 | ROV-117 will fail Open to vent the Run Tank
11.2.3 | ROV-300 will fail closed
11.2.4 | SOV-1 will fail open | | Normally open valve

Test Procedure MPV LN2 Testing ER33-TP-0146 Revision-Baseline Date: 6/29/2016 Page 22 of 24

Test Procedure LPS MFV Testing ER33-TP-0135 Revision-Baseline Date: 6/29/2016 Page 14 of 24

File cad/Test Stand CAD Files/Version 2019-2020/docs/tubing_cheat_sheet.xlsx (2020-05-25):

relevant standard:ASTM A269
LFETS tubing cheat sheet
 | tubing OD | wall thickness | bend radius (centerline) | minimum section length (straight) | minimum straight length at end
 | 0.250 | 0.035 | 0.750 | 1.750 | 1.250
 | 0.375 | 0.035 | 1.250 | 2.000 | 1.250
 | 0.500 | 0.049 | 2.000 | 2.250 | 1.313
 | 0.750 | 0.065 | 4.000 | 2.500 | 0.563 | <- shorter because nut can slide around 4" bend radius?
source |  | swagelok's Tubing Data Sheet MS-01-107 | NASA ksc-spec-z-0008d | NASA ksc-spec-z-0008d | NASA ksc-spec-z-0008d

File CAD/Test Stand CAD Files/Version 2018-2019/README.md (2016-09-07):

# liquid-engine-test-stand
A small liquid rocket engine test stand.

[Link to the EGSE requirements document (LFETS Dashboard)](https://docs.google.com/document/d/1tynERJ860UtjlAusS-HwE12AD3NaDbKgZLtqMx81SuI/edit?usp=sharing)

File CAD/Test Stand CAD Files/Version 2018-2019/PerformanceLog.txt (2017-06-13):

Mesh Preparation:  0 hr 0 min 0 sec
Standard solid mesh bolt head imprint and hard point processing:  0 hr 0 min 0 sec
Standard solid mesh total preparation including imprint:  0 hr 0 min 0 sec
Standard surface meshing for Solid Mesh:  0 hr 0 min 1 sec
Standard volume meshing for Solid Mesh:  0 hr 0 min 0 sec
Standard solid mesh arranging data:  0 hr 0 min 0 sec
Standard solid mesh total:  0 hr 0 min 1 sec
Beam mesh:  0 hr 0 min 0 sec
Mesh Preparation:  0 hr 0 min 0 sec
Standard solid mesh bolt head imprint and hard point processing:  0 hr 0 min 0 sec
Standard solid mesh total preparation including imprint:  0 hr 0 min 0 sec
Standard surface meshing for Solid Mesh:  0 hr 0 min 1 sec
Standard volume meshing for Solid Mesh:  0 hr 0 min 1 sec
Standard solid mesh arranging data:  0 hr 0 min 1 sec
Standard solid mesh total:  0 hr 0 min 4 sec
Beam mesh:  0 hr 0 min 0 sec
Preparing to transfer data:  0 hr 0 min 0 sec
Processing material properties:  0 hr 0 min 0 sec
Processing element groups:  0 hr 0 min 0 sec
Processing drop test gap nodes:  0 hr 0 min 0 sec
Updating thickness for shell regions:  0 hr 0 min 0 sec
Processing rconst for elements:  0 hr 0 min 0 sec
Processing egroups:  0 hr 0 min 0 sec
Transferring loads and boundary conditions:  0 hr 0 min 0 sec
Generating body pairs to check contact:  0 hr 0 min 0 sec
Generating contacts:  0 hr 0 min 0 sec
Number of Contacts: 0
Transfer SL1 data:  0 hr 0 min 0 sec
Generate more accurate contact data:  0 hr 0 min 0 sec
Number of contact data: 0
Transfer beam/joint contact data:  0 hr 0 min 0 sec
Transferring other special loads:  0 hr 0 min 0 sec
Transferring bearing loads:  0 hr 0 min 0 sec
Transferring mass elements:  0 hr 0 min 0 sec
Transferring point loads:  0 hr 0 min 0 sec
Transferring distributed beam loads:  0 hr 0 min 0 sec
Transferring rigid bodies:  0 hr 0 min 0 sec
Transferring component no penetration:  0 hr 0 min 0 sec
Writing Data:  0 hr 0 min 0 sec
Transferring analysis options:  0 hr 0 min 0 sec
Total midsurf mapping:  0 hr 0 min 0 sec

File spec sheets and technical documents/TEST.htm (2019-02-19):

Test Stand

Learning Outcome Desired

Project Management

Team Definition

ID | TEAM MEMBER | E-MAIL | NOTES
1 | Bertrand DeChanter | bdchant@pdx.edu
2 | Jacob Tiller | jtiller@pdx.edu
3 | Eric Thomas | emt3@pdx.edu
4 | Sam Hastings-Hauss | sdh3@pdx.edu
5 | Matthew Ng | ng7@pdx.edu
6 | Petr Mazhnikov | pam3@pdx.edu
7 | Erik Potenza | erik33@pdx.edu

Schedule

Requirement Gathering Phase

Project Goals

The goal of this project is to make fire.

Problem Statement

Supporting Images

Customer Definition

ID | CUSTOMER | CATEGORY | MOTIVATION
1 | Portland State Aerospace Society | Internal Customer | Amateur Rocket and Small Satellite Manufacturer
2 | Andrew Greenberg | Internal Customer | Head Advisor over Portland State Aerospace Society
3 | Mark Weislogel | Internal Customer | Head Advisor over liquid engine test stand capestone team
4 | Sung Yi / Faryar | External Customer | Instructor evaluating capestone team

Product Design Specification

Original Customer Requirements

Finalized Customer Requirements

ID | REQUIREMENT | CUSTOMERS
1 | 1. questions! | 1
2 | 2. Create a formal failure modes and effects analysis. | 1
3 | 3. Create a safety standard operating procedure. | 1
4 | 4. Create standard operating procedure | 1
5 | 5. Create a post firing analysis of engine with suggestions. | 1
6 | 6. Safety proceedures are known and followed. | 1
7 | 7. Isopropyl alchohol for fuel | 1
8 | 8. Liquid oxygen as an oxidizer | 1
9 | 9. Nitrogen gas as a pressurant | 1
10 | 10. Data acquisition equipment supplied from Portland State Aerospace society | 1
11 | 11. Create standard operating procedures. | 1
12 | 12. Create standard safety procedure. | 1
13 | 13. All members must participate in any mandated safety training. | 1
14 | 14. Incorperate the 2.2kN test engine supplied by Portland State Aerospace Society. | 1
15 | 15. Human interaction with the stand during testing must be minimized. | 1
16 | 16. No person(s) are to approach the test stand while system is pressurized. | 1
17 | 17. There must be a redundant system to prevent accidental pressurization of the system. | 1
18 | 18. Funds available from PSAS should not exceed $2,000 without prior approval. | 1

Link to the Technical Review Specifications

Engineering Requirements

Original Engineering Requirements

[Note that the same engineering requirement may appear more than once, if they are associated with more than one customer requirement.]

ID | REQUIREMENT
1 | 1.1: Answers!: Ideal = 100; Min = 50; Max = 150; Unit = IU
2 | 2.1: FMEA: Ideal = 1; Min = 0; Max = 1; Unit = FMEA
3 | 3.1: [List associated design variable]: Ideal = 1; Min = 0; Max = 1; Unit = [List unit]
4 | 4.1: [List associated design variable]: Ideal = 1; Min = 0; Max = 1; Unit = [List unit]
5 | 5.1: [List associated design variable]: Ideal = 1; Min = 0; Max = 1; Unit = [List unit]
6 | 6.1: [List associated design variable]: Ideal = 1; Min = 0; Max = 1; Unit = [List unit]
7 | 7.1: [List associated design variable]: Ideal = 1; Min = 0; Max = 1; Unit = [List unit]
8 | 8.1: [List associated design variable]: Ideal = 1; Min = 0; Max = 1; Unit = [List unit]
9 | 9.1: [List associated design variable]: Ideal = 1; Min = 0; Max = 1; Unit = [List unit]
10 | 10.1: [List associated design variable]: Ideal = 1; Min = 0; Max = 1; Unit = [List unit]
11 | 11.1: [List associated design variable]: Ideal = 1; Min = 0; Max = 1; Unit = [List unit]
12 | 12.1: [List associated design variable]: Ideal = 1; Min = 0; Max = 1; Unit = [List unit]
13 | 13.1: [List associated design variable]: Ideal = 1; Min = 0; Max = 1; Unit = [List unit]
14 | 14.1: [List associated design variable]: Ideal = 1; Min = 0; Max = 1; Unit = [List unit]
15 | 15.1: [List associated design variable]: Ideal = 1; Min = 0; Max = 1; Unit = [List unit]
16 | 16.1: [List associated design variable]: Ideal = 1; Min = 0; Max = 1; Unit = [List unit]
17 | 17.1: [List associated design variable]: Ideal = 1; Min = 0; Max = 1; Unit = [List unit]

Finalized Engineering Requirements

ID | DESIGN VARIABLE | IDEAL | MIN | MAX | UNIT | CATEGORY | SIGNIFICANCE | CUSTOMER REQ | INCLUDED IN OBJ. FUNC.?
1 | Answers! | 100 | 50 | 150 | IU | Function | | 1 | Yes
2 | FMEA | 1 | 0 | 1 | FMEA | Documentation | | | Yes

Explanations

Phase Review

ID | DESIGN POINT ENTITY | COMPLETED? (Y/N) | LOCATION (PATH)
1 | Project Goals | Yes
2 | Problem Statement | Yes
3 | Customer Definition | Yes
4 | Customer Interviews | Yes
5 | Customer Requirements | Yes
6 | Engineering Requirements | Yes

Gate Review

Conceptual Design Phase

Design Ideas

Canvas for New Design Ideas

Archived Design Ideas

Location of Design Sketches

Design Description

Designs Considered

Link to Documentation

Design Scoring

Scoring Tree

Test Stand

Scoring Guidelines

Design Selection

House of Quality

CUSTOMER NEED | CUSTOMER | IMPORTANCE
questions! | 1 | Unassigned
Create a formal failure modes and effects analysis. | 1 | Unassigned
Absolute Importance:
WEIGHTS:
MIN:
IDEAL:
MAX:
UNIT:

Decision Matrix

WEIGHTS:
CONCEPTS:

Design Overview

Overview

Summary

Design Selection

Confiderence

Further Rationale

Phase Review

ID | DESIGN POINT ENTITY | COMPLETED? (Y/N) | LOCATION (PATH)
1 | Sketches of Concept Ideas | No
2 | Narration Describing the Concept Ideas | No
3 | Analysis of Concept Ideas | No
4 | Concept Selection with Rationale | No

Gate Review

Detailed Design Phase

Risk Identification

Narration

Supporting Images

Model

Image Gallery

Explanations

Imported Settings

Full Path (Manual Insertion)

Root Directory (Automatic Extraction)

Calculations & Analysis

Analyses Conducted

Explanations

File Location

Phase Review

ID | DESIGN POINT ENTITY | COMPLETED? (Y/N) | LOCATION (PATH)
1 | Risks Identified | No
2 | Description of the Detailed Design | No
3 | Solid Model | No
4 | Analysis of Risk Factors | No
5 | Project Schedule

Gate Review

Final Design Phase

Narration

Supporting Images

Testing

Overview

Explanations

To be added

Requirement Validation

ID | DESIGN VARIABLE | IDEAL | MIN | MAX | UNIT | CATEGORY | SIGNIFICANCE | CUSTOMER REQ | INCLUDED IN OBJ. FUNC.? | SATISFIED? | METHOD | TEST RESULTS
1 | Answers! | 100 | 50 | 150 | IU | Function | | 1 | Yes
2 | FMEA | 1 | 0 | 1 | FMEA | Documentation | | | Yes

Bill of Material

Overview

File Location

Parts & Assembly

Drawings

Explanations

File Location

Manufacturing Options

Overview

Explanations

To be added

File Location

Cost Analysis

Phase Review

ID | DESIGN POINT ENTITY | COMPLETED? (Y/N) | LOCATION (PATH)
1 | Summary of Build Plan | No
2 | Test Plan | Yes
3 | Validated Requirements | No
4 | Bill of Material | Yes
5 | Parts & Assembly | No
6 | Analysis of Manufacturing Options | No
7 | Cost Analysis | No

Gate Review

Design Revisions

Appendix

References

Standards

Books

Papers

Patents

Websites

Other

Customer Interviews

DATE | CUSTOMER | INTERVIEWER | QUESTIONS | RESPONSE
2018-11-08 | 1. Portland State Aerospace Society | Bertrand DeChanter | What standard of safety must be met. | Safety proceedures are known and followed.
2018-11-18 | 1. Portland State Aerospace Society | Bertrand DeChanter, Jacob Tiller, Eric Thomas, Sam Hastings-Hauss, Matthew Ng, Petr Mazhnikov, Erik Potenza | What kind of documentation is needed? | Create a formal failure modes and effects analysis.
2018-11-18 | 1. Portland State Aerospace Society | Bertrand DeChanter, Jacob Tiller, Eric Thomas, Sam Hastings-Hauss, Matthew Ng, Petr Mazhnikov, Erik Potenza | What kind of documentation is needed? | Create standard safety procedure.
2018-11-08 | 1. Portland State Aerospace Society | Bertrand DeChanter, Jacob Tiller, Eric Thomas, Sam Hastings-Hauss, Matthew Ng, Petr Mazhnikov, Erik Potenza | What kind of documentation is needed? | Create standard operating procedures.
2018-11-08
2018-11-08 | 1. Portland State Aerospace Society | Bertrand DeChanter, Jacob Tiller, Eric Thomas, Sam Hastings-Hauss, Matthew Ng, Petr Mazhnikov, Erik Potenza | What is the budget? | Funds available from PSAS should not exceed $2,000 without prior approval.
2018-11-18 | 1. Portland State Aerospace Society | | What supplies will be needed? | Liquid oxygen as an oxidizer
2018-11-18 | 1. Portland State Aerospace Society | | What supplies will be needed? | Nitrogen gas as a pressurant
2018-11-18 | 1. Portland State Aerospace Society | | What supplies will be needed? | Data acquisition equipment supplied from Portland State Aerospace society
2018-11-08 | 1. Portland State Aerospace Society | Bertrand DeChanter, Jacob Tiller, Eric Thomas, Sam Hastings-Hauss, Matthew Ng, Petr Mazhnikov, Erik Potenza | What supplies will be needed? | Incorperate the 2.2kN test engine supplied by Portland State Aerospace Society.
2018-11-08 | 1. Portland State Aerospace Society | | What standard of safety must be met. | All members must participate in any mandated safety training.
2018-11-08 | 1. Portland State Aerospace Society | Bertrand DeChanter, Jacob Tiller, Eric Thomas, Sam Hastings-Hauss, Matthew Ng, Petr Mazhnikov, Erik Potenza | What standard of safety must be met. | Human interaction with the stand during testing must be minimized.
2018-11-08 | 1. Portland State Aerospace Society | | What standard of safety must be met. | No person(s) are to approach the test stand while system is pressurized.
2018-11-08 | 1. Portland State Aerospace Society | Bertrand DeChanter, Jacob Tiller, Eric Thomas, Sam Hastings-Hauss, Matthew Ng, Petr Mazhnikov, Erik Potenza | What standard of safety must be met. | There must be a redundant system to prevent accidental pressurization of the system.
2018-11-08 | 1. Portland State Aerospace Society | | What is the budget?

Meeting Notes

DATE | ATTENDEES | SCRIBE | AGENDA | MINUTES
2018-10-23 | Bertrand DeChanter, Jacob Tiller, Eric Thomas, Sam Hastings-Hauss, Matthew Ng, Petr Mazhnikov, Erik Potenza | Jacob Tiller | (Test) Discuss ecosystem requriement and how to incorporate with current project managment. | 1. Started then stopped talking

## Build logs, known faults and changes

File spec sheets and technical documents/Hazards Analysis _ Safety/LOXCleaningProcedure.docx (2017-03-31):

LOX Cleaning Procedure

Necessary Items:

KimTech Clean Wipes

Disposable Gloves

Dawn Soap

Distilled Water Bottle

IPA Bottle

Heavy Duty Aluminum Foil

Plastic Baggies - Varying Sizes

Procedure:

1. PUT ON GLOVES. Do not touch the parts with bare hands--you will contaminate them with fingerprint oils.
2. Clean the part with Dawn & Distilled water to remove any visible contaminant.
3. Soak a kimtech wipe with IPA & polish the part until it’s totally clean. For tubes, ramrod KimTech wipes through until clean.
  a. For small parts, o-rings, or pieces with intricate spaces which are hard to reach, use the ultrasonic cleaner filled with IPA.
  b. Remove from the ultrasonic cleaner with gloves and/or tongs--DO NOT TOUCH WITH BARE HANDS.
4. Use a clean, dry Kimtech wipe to dry the part as best as you can.
5. Set the part on top of a fresh Kimtech wipe in the “cleaned parts” area.
  a. Leave overnight so IPA fully evaporates.
6. WEAR GLOVES while removing the part from the clean area. Wrap part in heavy duty aluminum foil & place into a baggie.
7. LABEL the baggie with the part number/identifying information, as well as “LOX CLEAN--DO NOT TOUCH.”
8. Place the part in the appropriate storage area.

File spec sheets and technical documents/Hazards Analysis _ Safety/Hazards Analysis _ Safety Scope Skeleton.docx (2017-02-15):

Cryogenic Dangers:

- Asphyxiation
- Thermal Expansion
  - Pressure relief valves usually set at 90% to 105% of MAWP, burst disk at 110%
- Skin Damage
- Others, I’m sure.

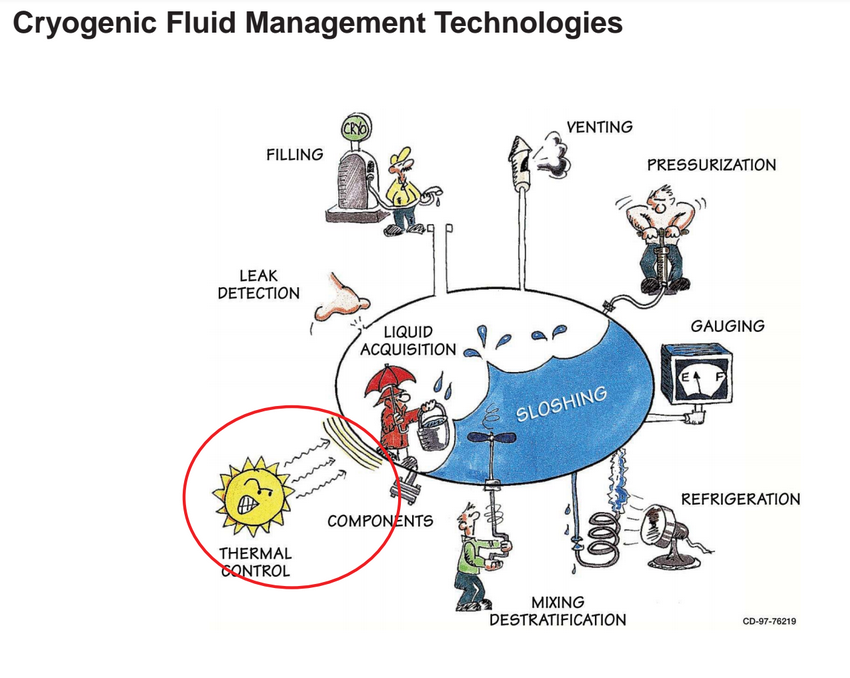
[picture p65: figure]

Considerations:

- Hazard Analysis Report
  - Hydro Test http://www.dudgeonjacks.com/HYDROSTATIC.html I got the Model 4A and it makes it really nice to do hydro testing. People claim grease guns work but I could never get them to work without leaking and making a huge mess. Just be sure to get rid of all the air and only have liquid when you hydro test in case you burst something. It's also a good idea to put something between you and the test article, like a brick wall, earth, etc.
- Storage
  - Storage: A normal welding cylinder should be fine in the garage. Millions of people with a lot less sense than your average aRocket reader store their oxy/acetylene bottles under pressure in the garages for years and you don't hear too much about it. The main thing is that I always remove the regulator and put the protective cap on it so if it falls over, it will stay intact.

Overpressurization. - NASA

Oxygen cannot be kept liquid if its temperature rises above the critical

temperature of -118.6 °C (-181.4 °F). Consequently, if LOX is trapped in a closed

system and allowed to warm, extreme pressures can overpressurize the system.

For example, LOX trapped between valves can rupture the connecting pipe.

Pressure relief of some kind must be provided where trapping might occur.

Moreover, relief and vent systems must be sized to accommodate the flow so that

excessive backpressures will not occur. Cryogenic liquid storage vessels are

protected from overpressurization by a series of pressure relief devices. These

relief devices are designed to protect the inner vessel and the vacuum-insulated

portion of the tank from failures caused by inner and outer shell damage,

overfilling, and heat load from insulation damage or from a fire.

(1) In specific instances, such as when these vessels are involved in a fire

which impinges upon the ullage area of the tank, container failure could

result. In these instances, water should be directed onto the flame-

impinged portion of the tank to allow the tank to cool. Enough water

should be directed onto this area to keep the tank wet. Water should not be

directed toward the relief devices, as the venting gas may cause the water

to freeze and seal off the relief device.

(2) Frost appearing on the outer wall of an insulated cryogenic vessel is

indicative of vessel insulation loss. Frost appearance is only a clue to the

type of insulation loss. This insulation loss could be caused by a

movement of the insulation in the annular area of the tank, by loss of

vacuum in the annular area, or by inner vessel failure. Assistance from

knowledgeable and responsible pressure-systems personnel should be

obtained.

(a) Personnel should listen and watch for indication of pressure-relief

device actuation. Constant relief actuation is an indication that a

major problem has occurred. Special care should be taken if the

sound of the relief device changes and becomes higher pitched

while operating.

(b) Continued pressure rise while the relief device is actuated indicates

a major system malfunction. If constant relief device actuation is

occurring, immediately evacuate the area and physically rope off

and control the area if this can be performed safely. Venting the

vessel is recommended, if possible. Do not apply water, as this

would only act as a heat source to the much colder oxygen and

aggravate the boiloff.

- Insulation
- Test Stand
  - Procedures for:
    - Filling
    - Liquid nitrogen testing?
    - LOx and Ethanol firing
    - Purging Lines
    - Git: https://github.com/psas/liquid-engine-test-stand/issues/21
  - Igniters See NASA Technical Memorandum 106493 (Hydrogen-Oxygen Torch Ignitor). Has lots of cross-section drawings of ideas how to mount it to an engine (axial, sideways, angled, etc.) For your GOX inlet, don't place your restricting orifice right at the point of injection into the igniter. The GOX jet will come out too fast and erode the opposite wall. Even having it as little as 0.25 inches upstream was enough to solve my erosion problem. I used a 0.032 inch (I think) precision orifice but a 0.060 inch orifice into the igniter chamber. My fuel orifice was 0.008 inches - it has to drop a lot more pressure than the GOX, plus it is a liquid not a gas.
  - Regulators: I too had trouble finding an inexpensive GOX regulator that could go above 200 psi. I ended up ordering a Victor TPR250-500-992 where the -992 is supposed to be for a CGA992 British oxygen fitting. The regulator arrived and had "inert gas" stamped on it. I called Victor and spoke to one of their customer support guys who said the inert and oxygen cleaned regulators have the same parts and go through the same cleaning process. He said there just isn't much demand for GOX regulators above 200 psi so that's why they don't carry them in the welding line. I managed to use mine up to 350 psi but that's just my experience with this one regulator. On valves and regulators, just make sure all seals are oxygen compatible (Viton, PTFE, etc.)
  - Firing: I usually wait a few minutes after running. If you have a temperature sensor on your motor, you can watch it until it cools down.
- Cleaning
  - Cleaning: This has been discussed before on aRocket (I asked similar questions). Disassemble everything, clean everything in a solvent (some use IPA, I use acetone), use cotton swabs for cleaning the threads, etc., then I end up washing in Dawn soap and distilled water. Dry it all out and reassemble with GOX compatible grease (Krytox). I only clean parts when I suspect contamination or if I've run water through the lines (water drops turn to steel at LOX temperatures).
  - Lubricants, Gaskets & Seals – See NASA Propulsion Test Handbook on Drive
    - OmniSeals?

1) Plumbing Parts in contact with GOX:

a. Regulator: what type of regulators are people using for GOX? From looking on McMaster I can see that most GOX regulators run to about 200 psi.

Any pressures higher than this get quite expensive. Are people running

engines GOX with a higher pressure? If so what types of regulators are being used? Any issues running engines at such low pressures besides the obviously larger size?

You can use any regulator with materials and seals that are oxygen

compatible. Figuring out what black o-rings are made out of, or what's

in a sealed part of a regulator, is about the most difficult part.

Looking for stuff that is used in high pressure air for SCBA use is a

good start. 6000psi air has many of the same hazards as high pressure

GOX. Aqua Environment makes reasonably priced gas hardware, which you

can buy through Aerocon Systems.

b. I can purchase a solenoid valve that is cleaned for oxygen use but most other parts: eg. connectors, tubes, filters, check-valves, etc… are not. What approaches do people recommend for cleaning parts (on a limited

budget)? Also, how often should parts be cleaned (eg. after every test, only when the plumbing is opened up to the atmosphere or could have become contaminated, etc…)?

You can send stuff off to be lox cleaned, but that's less common in

the hobby world. There they use a series of different solvents to

clean out everything.

The abbreviated process for amateurs is as such:

1. Clean the part with soap and water to remove any dirt or grease or

other visible contaminant. Use whatever is handy to mechanically

clean, as long as it doesn't leave a residue like fibers.

2. Clean the part with pure isopropyl alcohol (IPA) until clean. For

small parts like bits of a regulator or o-rings, easiest is an

ultrasonic cleaner. For tubes, ramrod through kimwipes soaked in IPA

until they come out clean.

3. Remove the IPA by letting air dry in a clean area, baking at

whatever temperature the part will withstand, or putting under vacuum.

Hook up a good filter to a good air supply (or use nitrogen bottles

through a clean regulator) to blow parts dry and blow out tubing.

4. Store parts until needed with clean caps, or wrap in aluminum foil.

Household heavy duty aluminum foil is effectively lox clean.

If you flare the tube after cleaning it, re-clean the flared ends

before use. Clean AN and Swagelok nuts and fittings, even though

they're not supposed to touch the working fluid, because leaks will

touch them. You don't want lox spiraling out threads full of oil.

When reassembling, use oxygen compatible lubricants. The manufacturer

of the regulator will often have recommendations for that, but

Dupont's Krytox line is a common substitute for just about anything.

It's not a great lubricant, but there aren't many gox/lox compatible

ones out there.

Professional lox cleaning companies use IPA as the last step, so it's

what I stick with. Earlier in the process they also use other acids or

bases to degrease stuff they can't get at.

Re-clean when you think the part is contaminated. Re-cap stuff when

you disassemble so it stays clean, exposure to air is not

contamination. Using ethanol, you're pretty safe against unexpectedly

durable residues.

- Transportation
  - Transportation: It really shouldn't leak but I wouldn't sweat a short trip in the car. A pickup (strapped down!) would be better though. Those DOT rated cylinders are really tough.
  - Section 801 e of NASA Doc.

Transport Requirements for Liquid Oxygen.

General requirements for the transport of LOX are given in 49 CFR 172.101

(1986), Hazardous Materials Table, and 49 CFR 173 (1986), Shippers-General

Requirements for Shipments and Packaging. The proper shipping name for LOX

is Oxygen, refrigerated liquid (cryogenic liquid).

(1) Packaging must be labeled NON-FLAMMABLE GAS, OXIDIZER.

(2) Packaging requirements are given in 49 CFR 173.316 (1986), Cryogenic

Liquids in Cylinders, 49 CFR 173.318 (1986), Cryogenic Liquids in Cargo

Tanks, and 49 CFR 173.320 (1986), Cryogenic Liquids, Exceptions.

Specifications for the qualification, maintenance, and use of cargo tank

motor vehicles are covered in 49 CFR 173.33 (1986), for the design of

insulated cargo tanks in 49 CFR 178.338 (1986), and for the loading and

unloading of cylinders in 49 CFR 177.840 (1986), Class 2 (gases)

Materials.

(3) Liquid oxygen is not permitted aboard passenger aircraft, passenger

railcars, or cargo aircraft. It may be stowed only above deck on cargo

ships.

Section 802 b: Noncommercial Equipment and/or Special Operations.

Special equipment or operations used for the transport of oxygen must meet federal and state labor requirements (29 CFR 1986) as well as additional requirements of the cognizant NASA authorities.

Section 802 c: Guidelines for the Design of Noncommercial Transport Equipment.

(1) General guidelines. Where applicable, standard oxygen design practice

should be used (Chapters 3 and 4).

(a) The tankage design will be in accordance with accepted design

practice (ASME 1995a, b).

(b) Redundant relief protection must be provided to the tank and

piping systems.

(c) The design of the undercarriage shall isolate the tank and piping

systems from potential collision damage.

(d) Controls should prevent oxygen venting while the vehicle is in

motion.

(e) The trailer should use a fail-safe emergency brake system.

(2) Requirements for highway service. The design of noncommercial vehicles

must comply with federal and state transportation guidelines (see 801

above) for operation on public thoroughfares. In addition to the general

guidelines above, the design must meet highway standards for cargo tank

design (49 CFR 178.338 1986 for cryogenic transport and 49 CFR

178.337 1986 for gas carriers).

802 D: General Operating Procedures.

The following guidelines apply to all oxygen transport operations.

(1) General.

(a) Operational areas should remain clear of nonessential personnel.

Appropriate personnel protective equipment should be used.

Facilities should maintain necessary deluge systems.

(b) Transport systems should be adequately grounded.

(c) The operational area should be kept free of combustible materials.

Spark-producing and electrical equipment that is within the

operational area and is not hazard-proof should be turned off and

locked out. All tools used shall comply with established safety

requirements.

8-5

(d) All tank inlets and outlets, except safety relief devices, should be

marked to designate whether they are covered by vapor or liquid

when the tank is filled.

(e) The temperature of LOX is so low that liquid air will form on

uninsulated transfer equipment and vaporizers. Drip pans should

be installed under all such equipment. The concern is that LOX

will come off separately from LN2 as the liquid air returns to a gas.

Oxygen will vigorously support combustion of any materials such

as paint, oils, or lubricants that make up the cargo tank or may be

found on the ground.

(f) Trailers shall be equipped with a dry-chemical fire extinguisher.

The rating shall not be less than 10 BC.

(g) In the event of a oxygen leak the transfer must be stopped and the

leak repaired. In the event of a fire the oxygen sources should be

isolated as quickly as possible.

(h) Operational procedural checklists should be used.

Note: LOX forms shock-sensitive explosive compounds with

carbonaceous materials. Transfer operations should not be conducted

over asphalt surfaces or porous surfaces such as sand that may hide

the presence of oils and greases.

- PPE
  - Distance: I'm a bit conservative here but assume the worst case of the motor detonating and ask yourself what needs to be in the way. I use 1 inch Lexgard blast shield around the motor and then I have the whole assembly in a 4 foot earth pit with a berm on the sides. But that's for the large motor testing (100-250 lbf). For igniter testing (1-2 lbf), I use the blast shield and get behind the brick wall of the side of my garage.
  - Clothing: cotton only - synthetics tend to fuse to your skin when melted. Cotton just chars away. And no goop in the hair either. I use regular safety glasses and also a face shield when working with LOX.
  - Responses from Ben Brockert:

Clothing/Eye Protection:

a. What sort of clothing protection is recommended?

Always safety glasses. When working with LOX, also a face shield,

which is always worn with safety glasses. A long sleeve shirt and long

pants is a good idea, natural fibers or specifically fire-resistant

only. McMaster has a variety of flame-resistant coveralls and

- jumpsuits.
- Again, I'm really glad you're worried about this, but over time you
- will likely get less worried. Somewhat with cause, and somewhat just
- because you've always been lucky. I've seen "professionals" do things
- like walk through puddles of LOX or cool themselves off by sticking
- the LOX tank exhaust into their clothes. Don't be that guy.
- But they almost always get away with it, until someone blows off their
- foot. I'll admit that I've touched LOX on more that one occasion.
- With high pressure GOX, the pressure is probably more a hazard than

the ox. Watch out for damaged hoses.

Nasa and others have GOX and LOX safety publications, googling around

for them is a good idea. That said, one talks about the procedure for

doing lox transfers on asphalt, which is simply something I never

would design into my process. So don't take them as always

authoritative.

- Fail modes – relief valves/venting
  - Burst Discs http://www.oseco.com/products/holders-and-accessories/threaded/ You can use a standard disc and holder (recommended) or have a custom disc made and build your own holder (like I did but was a lot of work). Pressure relief valves work too but they can stick, especially if exposed to cryo temps. Burst discs are super simple and guaranteed to work. Be sure to point the burst disc vent away from any nearby people when doing test stand checkout. They can fatigue and fail early (surprises the heck out of you...)
  - Identify LFE testing computer system control loop characteristics - https://github.com/psas/liquid-engine-test-stand/issues/6
- Testing – Permits, City Ordinances, etc.
  - See manual (template) for launch and apply it to test stand.
  - Ensure compliance with
    - ASME,
    - Cryo handling,
    - Boiler Code, etc.

aRocket archives
In addition to the Freelists archive, check out:
http://blastzone.org/aRocket/arocketlogin.asp
These go back to 1995 and have a lot from the early days of Armadillo, Masten, XCOR, etc.

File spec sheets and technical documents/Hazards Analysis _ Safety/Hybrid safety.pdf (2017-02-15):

Technical papers

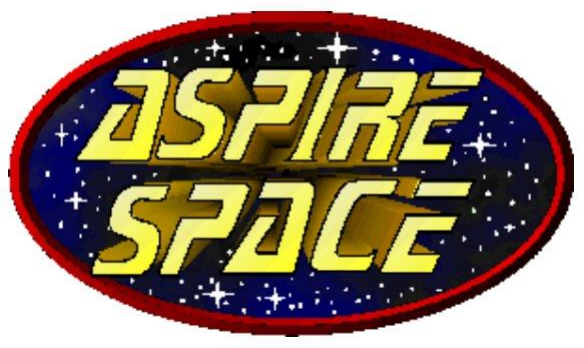
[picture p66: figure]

Author: Rick Newlands | 1 | updated: 06/11/16

# Hybrid safety

## Aspirepace technical papers Author: Rick Newlands

Technical papers

Author: Rick Newlands | 2 | updated: 06/11/16

## Table of Contents

Fire 12

CTN 24

Technical papers

Author: Rick Newlands | 3 | updated: 06/11/16

Technical papers

Author: Rick Newlands | 4 | updated: 06/11/16

Technical papers

Author: Rick Newlands | 5 | updated: 06/11/16
Iron | 49
Cadmium, beryllium, magnesium and Mercury | 49
Surface preparations | 49
Materials compatibility: nonmetals | 49
Recommendations | 50
Part 5: High-Test Peroxide (HTP) safety (Ref.s 24 - 43) | 51
Physical properties | 51
Decomposition | 52
Corrosion | 53
Home-brew | 53
Passivation and cleaning | 53
Storage | 55
Venting | 56
Handling | 57
Transportation | 57
Light sensitivity | 57
Spillages | 57
Small spill | 57
Large Spill | 57
Disposal/drainage of HTP | 57
Fire raising potential | 58
Fire extinguishing media | 58
Vapour phase explosion | 58
Oxygen enrichment of the vapour phase | 58

Condensed phase explosibility without organics (as a mono-explosive: purely on its own)

(Ref. 39, Solvay Interox, Inc) | 59
Condensed phase explosibility with organics | 59
Hazards to human health | 60
Potential acute health effects | 60
Potential chronic (long term) health effects | 61
First Aid Measures | 61
Notes to Physician | 61
Engineering Controls | 61
Protective Clothing | 61
Materials compatibility | 62
Testing for compatibility (Ref. 24) | 62

Technical papers

Author: Rick Newlands | 6 | updated: 06/11/16
Compatibility class | 64
Aluminium | 64
Stainless steel | 65
Other metals | 66
Surface finish | 66
Dissimilar metals | 66
Plastics | 66
Ceramics | 67
HTP is incompatible with | 67
Explosion hazard | 68
HTP will react explosively with hydrocarbons (fuels) | 68
Autoignition hazard | 68
Welding and soldering | 68
Filters | 69
Pumps | 69
Instrumentation | 69
Lap joints | 69
Lubricants | 69
Platings | 69
Brazing or silver soldering | 69
Hybrid design | 70
Recommendations | 70
Part 6: additional safety issues | 71
Engine firing safety | 71
Firing procedures | 71
Test-site safety | 71
Safety ethos | 71
Failure tolerance | 71
Engine firing inhibits | 71
Ignition safety | 71
Blockhouse | 72
Engine system testing | 73
Training | 73
Tools | 73
Human factors | 73
Electrical | 74

Technical papers

Author: Rick Newlands | 7 | updated: 06/11/16
Data logging | 74
Software | 74
Test site cabling | 74
Test site lightning protection | 74
Graphite nozzles | 75
Fluorinated lubricants and fluoroplastics | 75
Glossary: | 76
References: | 78

Technical papers

Author: Rick Newlands | 8 | updated: 06/11/16

### Introduction

“Rocketry success demands perfection…the first to feel this awesome imperative for perfection are the propulsion systems, especially the engines. Unless they operate flawlessly first, none of the other vehicle systems will get a chance to perform” Wernher von Braun.

While there is no doubt that hybrids are considerably safer than traditional solid or liquid rocket engines, there is a popular misconception that they are totally safe, and never go boom. Sadly, an ill-designed hybrid, or one that is subject to mechanical abuse, will most certainly go bang. Several have, and lives have been lost.

The following is a guide to some of the issues concerning the safe design and operation of amateur hybrids, focusing on the ‘green’ (non-toxic) oxidisers: nitrous oxide, liquid oxygen, and high-test (high-strength) hydrogen peroxide.
Note that Aspirespace has no hands-on experience with hydrogen peroxide.

Needless to say, in these days when uncurbed litigation is the biggest threat to democracy and the pursuit of happiness, we have to state that the following is solely our opinion, and we accept no liability whatsoever for accidents arising from following the advice herein, nor do we assume liability due to errors contained within this paper.

This edition has greatly benefitted from reference 1, which is highly recommended, and from the good folks on the Arocket rocketry forum.

Items in bold are referenced in the glossary at the end of this paper.

What is a hybrid?
A hybrid, as the name suggests, is an engine that shares components from both solid-propellant rocket and liquid-propellant rocket design.

A tank supplies liquid or gaseous oxidiser into a combustion chamber that contains a solid fuel; the term here literally meaning fuel only. In a ‘reverse hybrid’ system, a liquid fuel is injected, and a solid oxidizer is in the chamber.

The hybrid we’re all familiar with is the log fire: the rate at which the solid fuel burns depends upon the draught of gas passing over the surface of the wood, which you can increase by opening-up the flue on the chimney, to increase performance.

In a typical hybrid, the oxidizer flows down a hole, or ‘port’ running down the centre of a thick-walled pipe of solid propellant fuel.

Once the hybrid has been ignited, some of the hot combusted gas is carried by the port flow to the surface of the solid grain where its heat is transferred into the top layer of this fuel by forced convection.

The heat then melts and vapourises a layer off of the exposed surface, which then gets carried off into the port flow, where it burns in a rather interesting way; it actually burns in a narrow zone within the boundary layer known as the flame zone or flame sheet, which is at a depth between the fuel-grain below and the oxidizer flow above that is close enough to stoichiometric (best mix) to support combustion.

Technical papers

Author: Rick Newlands | 9 | updated: 06/11/16

### Part 1: oxidizer choice

The propellants used in hybrid motors encompass all the familiar ones, plus some that may be new to you.
Though in today’s world, the choice of oxidizers are increasingly being restricted to the more environmentally friendly ones: oxygen, High-test peroxide, and nitrous oxide.

As far as rocketry performance is concerned, hydrogen peroxide or just raw oxygen give better Specific Impulse and Density Impulse (packageability) than nitrous oxide (‘nitrous’), but nitrous is so much more user-friendly than these, which is why it’s so popular. The United Kingdom Rocketry Association’s safety code (version 5, section 5.2 gives some excellent advice on nitrous hybrid usage and safety. (www.ukra.org.uk)

One of the challenges in educating people about the dangers associated with oxidisers is their prior perceptions: oxygen is used in hospitals to make you better, nitrous is used by dentists, peroxide is used as a hair dye. These can lull you into a false sense of security when you begin your hybrid rocketry, but beware. Oxidisers can bite! Having said that, they can be handled safely provided you take all necessary precautions. I’ll try to outline many of these precautions in this article.

First off, nitrous oxide is not highly reactive to humans like hydrogen peroxide, nor excessively cold or excessively shock-sensitive like liquid oxygen (Lox).

Nitrous is, however, a powerful anaesthetic and is used as such by the medical profession: inhale too much and you might never wake up again.
Inhale Lox or peroxide vapour, and say goodbye to your lungs: terminal frostbite or combustion.

You can carry bottles of nitrous in the back of vans (but not in cars, there should be a barrier between driver and bottle in case of a leak as nitrous is a powerful anaesthetic; stupidly we’ve all done it, but keep all windows open.) Unless you want to be flame-grilled in an accident, you’d be crazy to carry Lox or peroxide in your own vehicle; they have to be pre-delivered to a proper test-site or launch-site which adds to the cost.

This table outlines some performance pros and cons to consider when choosing between oxidisers for hybrid applications. Safety issues will be discussed presently.

| Liquid oxygen | High Test Peroxide | Nitrous oxide
Composition | O2 | HTP | N2O
Vapour-pressure | Low: needs pumped | Low: needs pumped | 55 Bar at room temperature: self-pressurising
Typical oxidiser to fuel ratio | 2.5:1 | 6:1 | 7:1
Density (kg/m³ ) | 1140 | 1414 | Around 800 (liquid phase)
Storage | Cryogenic (boil-off rate) | Chemically reactive (passivation) | Inert (anaesthetic)
Flame temperature | High: One-shot graphite nozzles | Moderate: graphite nozzles can be reused. | Moderate: graphite nozzles can be reused many times.
Vacuum ISP with plastic fuel (seconds) | Highest (315) | Middle (290) | Lowest (230)
Mixture sensitivity | High | Low | Low
Stored just below the Critical temperature? | No, colder | No, colder | Yes

Technical papers

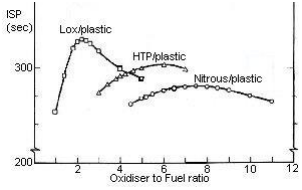
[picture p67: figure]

Author: Rick Newlands | 10 | updated: 06/11/16

Vapour pressure:
Liquid oxygen and peroxide require external pressurization; either from a separate gas supply or by using a pump. In contrast, nitrous oxide self-pressurises to a respectable 55 bar at room temperature.

Typical mixture ratio:
Liquid oxygen has a much more equal mixture ratio than peroxide or nitrous but this means that a Lox hybrid’s fuel grain is disproportionately larger than the other two: which have smaller fuel-grains but larger oxidizer tanks.

Plastic fuel grains tend to end up long and thin, giving long, thin, and so structurally inefficient combustion chambers. This mitigates against Lox-plastic hybrids.

Density:
Nitrous suffers here, requiring large, heavier pressurized tanks.

Storage:
The White Knight carrier aircraft took around an hour to climb to altitude and then release Spaceship One: if its hybrid had used Lox, a lot of it would have evaporated by then.

Flame temperature:
The combustion chamber temperature of a Lox hybrid is a lot higher, causing material problems.

Mixture ratio sensitivity:
Lox is much more sensitive to the wander of oxidiser to fuel mixture ratio that occurs during a hybrid burn as this graph of specific impulse (ISP) shows:

In many ways, nitrous oxide behaves as a slightly feebler, but user-friendlier peroxide; infact the technologies developed for peroxide rocket engines are applicable, including catalytic decomposition.

Peroxide itself is a popular hybrid choice; Richard Brown developed a very successful man-rated peroxide hybrid for his attempt on the motorcycle land-speed record, and currently the Bloodhound SST supersonic car is due to be powered by a peroxide hybrid.

Storing/filling oxidisers
Store fill tanks out in the open, and keep all plumbing above ground to aid leak detection. Have a source of water nearby for firefighting/deluge/dilution.

Technical papers

Author: Rick Newlands | 11 | updated: 06/11/16

Cleanliness
…is next to godliness as they say. For oxidiser systems this is imperative, as most contaminants are at the very least fuels, and often will cause an explosive compound with oxidisers. Use special degreased tools, and only use those tools for the oxidiser system alone. Use lint-free cloths, and avoid creating metal particles/swarf. Degreasing hybrid plumbing is dealt with later in this article.

Training
The safe use of rocketry oxidisers is all about education. The rocket firing team must all be trained to handle the oxidiser being used, understand its chemistry, its materials compatibility and non-compatibilities (potential to go boom with certain materials), and be aware of all safety implications. Getting them all to read this document is a good start, and then a safety document (Standard Operating Procedures, SOP) specific to your hybrid engine needs to be written and read.

The SOP should include:
- Notification of the designated safety authority during hazardous operations (The site safety officer).
- Protection of personnel.
- Prevention and detection of oxidiser leaks.
- Elimination of ignition sources.

The design of safe facilities and equipment should consider human capabilities and the limitations of personnel responsible for operations: your team are probably volunteers.

The firing tem need to demonstrate proficiency in the use and care of protective equipment and clothing and safety equipment, and also proficiency in maintaining a clean system and clean equipment in oxidiser service

Hazards analysis
Perform a hazards analysis on the hybrid engine system, particularly the oxidiser
components:
- Determine the most severe operating conditions (pressure, temperature, flow velocity, rubbing of components).
- Evaluate the flammability of the plumbing materials when in use. Test unusual materials for flammability.
- Evaluate potential unwanted ignition sources: flammable materials can only be used in sections of the plumbing where there is absolutely no chance of ignition.
- Be cautious of single-barrier failures: a single-barrier failure is a leak in which only the primary containment structure is breached. Such a leak introduces oxidiser into a region not normally exposed to oxidiser. The materials or configuration of parts in this region may not be compatible with oxidiser! Single-barrier failures are often overlooked, but the potential for component-part failures, such as diaphragm failures, can cause hazardous oxidiser-enriched environments, and can cause a substantially increased risk of ignition near electrical components for example.
- Attempting to correct single-point failures simply through procedural actions is not a reliable method. Design the system safe instead.
- Include hazards associated with contamination.
- Review secondary hazards, such as seal leakage to electrical equipment.
- Design equipment so that power losses, control pressure leakage, or other loss of actuation sources, return the equipment to a fail-safe position to protect people and property in the event of an accident.

Technical papers

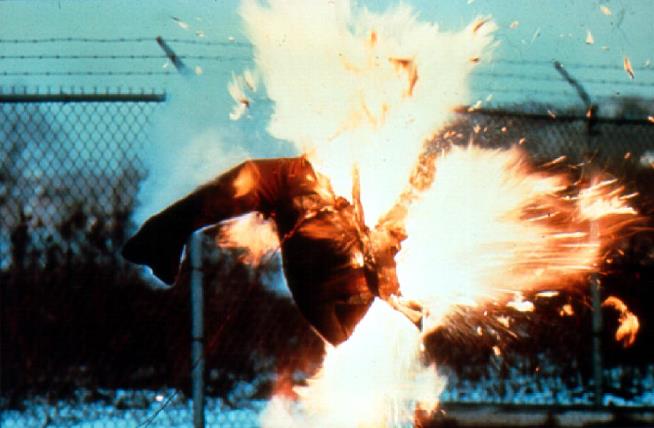
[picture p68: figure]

Author: Rick Newlands | 12 | updated: 06/11/16

Fire
One of the main hazards of oxidisers is their ability to create a fire. All three sides of the triangle must be present: a fuel, the oxidiser, and an ignition source. But with rocketry oxidisers, the fuel could even be metal pipework, and the ignition source a tiny spark from static electricity, friction, or simply dropping something heavy onto a pool of oxidiser soaked into the ground (which is then the fuel).

The key to the proper use of rocketry oxidizers is the use of compatible materials and the elimination of ignition hazards.

Humans and their clothing burn really well when splashed with oxidiser:

You have been warned! (the picture is of a cotton shirt splashed with Lox).

Technical papers

Author: Rick Newlands | 13 | updated: 06/11/16

### Part 2: pressure vessel and plumbing mechanical safety

Manual versus remote fill as it affects propellant tanks
Any container that can safely withstand the pressure without bursting will do for a propellant tank.

Stand next to a vessel pressurised full of high-pressure gas or vapour however, and your delicate bits are right next to a potential grenade; it’s the shrapnel of the exploding casing of a grenade that does the ripping through everything bit.

The United Kingdom Rocketry Association (www.ukra.org.uk ) quite rightly regards standing anywhere near a cylinder under pressure as potentially hazardous. Their safety code only allows people to be close enough for them to manually fill a tank if the tank is deliberately designed with a high margin of safety to prevent bursting.

Commercial hybrids are available such as the Aerotech manually-filled nitrous hybrid system which has this kind of strengthened tank, but for experimental hybrids UKRA will rightly require sufficient proof of tests performed to verify the tank safety if anyone is to be near it. Remote-controlled filling of flight tanks is preferred.

It doesn’t really need saying, but any homemade tank from a rocket that has suffered a recovery-system failure needs re-tested.

Aspirespace’s smaller vehicles (FLARE, ADV2a, and ADV2c/Rickrock) utilise manual fill.

Remote-filled systems allow the luxury of smaller tank safety margins, and so thinner-walled, lighter tanks, but the potential mass saving if using an ultra-thin tank is proportionately smaller as the vehicle diameter gets smaller.

For example, the number of fabric layers of a composite tank is an integer, it can’t be a fractional number, so small composite tanks can’t be made with an optimum composite thickness; they’re over-heavy.

Similarly, small aluminium tanks suffer minimum gauge problems, and over-proportionally large bolt-holes which raise stress.

Electroformed (grown metal) metal tanks can be made exceedingly thin, but annoyingly the electroformed metals are often incompatible with oxidisers (okay for Lox, all incompatible for nitrous).

A manual fill system is simpler to construct, but involves a higher level of design and testing of all tanks and plumbing that will be pressurised; safety of the filling crew is the prime consideration.

Obviously, you can safely be close to the massively over-strengthened tanks used to transport nitrous or Gox from the suppliers; they’re properly engineered and manufactured to allow you to move the contents around the country after all, and they’re tough unless you drop them on their necks and break the valve off. Then you get a rocket alright: seriously, the tanks can fly at very high speed and cause serious damage.
Such a commercial container is safe enough to handle (though not idiot-proof) but is far too heavy to fly.

Thin-wall aluminium tanks
So just how strong do propellant tanks have to be to be reasonably safe to be near without being too heavy to launch?
Military missile-design literature recommends a design safety factor of at least 2.0 times expected internal pressure on pressure-vessels that are to be manually handled while they’re pressurised.

Technical papers

Author: Rick Newlands | 14 | updated: 06/11/16

But this applies to a production tank; the fundamental point is that a batch of military production tanks have been tested to destruction to ensure that they really do burst at well over the 2.0 safety factor, and not a worrying 2.00001

Now we amateur groups don’t tend to make batches of tanks, therefore we can’t perform a suitable number of destruct tests.

Several rocketeers over the decades, making one-off tanks, have learnt to their cost that homemade thin-walled tanks, especially aluminium ones, need a burst safety-factor of at least three to handle the inevitable dings, scratches, and accidental alteration of the metal properties (typically inadvertent annealing) during manufacture.

Unexpected stress raisers can cause ally to rip apart at much lower average stresses than you bargained for, especially if you try welding the 6000 T series aluminiums, as this locally kills their heat treatment which is what originally made them strong. They must be re-tempered.

So for manual filling, then Aspirespace’s approach, based on the personal experiences and advice from engineers who make home-made tanks, is that you should design your hybrid’s one-off tanks to ensure that they safely withstand three times the maximum expected operating pressure (MEOP) without yielding. For nitrous oxide this would be three times the vapour-pressure of nitrous on a hot day, or 3 times 60 Bar = 180 Bar.

You should design the tank to fail in the safest way possible: popping the end-caps off rather than bursting the wall.

Having designed the tank to three times MEOP, you would then ‘proof’ test the tank to twice MEOP (a hydro-test: see below).

CO2 paintball-gun tanks, for example, are designed to be carried around during such adult tig-tag, bashed off trees, and people have sometimes fallen on them, without injury. These tanks are all pre-tested to around five times the expected internal pressure (of CO2, which has a higher vapour-pressure than nitrous), and are stamped to say as much; so a bad batch will fail during factory testing well before reaching the shops.

So Aspirespace have been comfortable enough with manual filling of nitrous hybrids that use such paintball tanks, such as our highly successful FLARE and ADV2 vehicles.

Paintball tanks are a good safe choice, but they’re somewhat overheavy. Also, most (Luxfer) paintball tanks use an imperial UNF internal thread on their necks; sourcing a suitable tap can be tricky.

DIY aluminium thin-wall tanks are often formed from end-domes and cylinders welded together. The 6000 series aluminiums are usually heat-tempered (designation ‘T’) and when welded lose this temper and so lose considerable strength. The tank therefore needs a post-weld heat treatment to restore the temper. The 2000 series aluminiums, though weaker, are not tempered so avoid this problem. Another way to get around this problem is to add extra metal around the joint: this lowers the stress in the metal so that the loss of strength isn’t an issue. This strengthening band is shown here in cutaway, and forms a useful tank skirt for attachment to the rest of the vehicle:

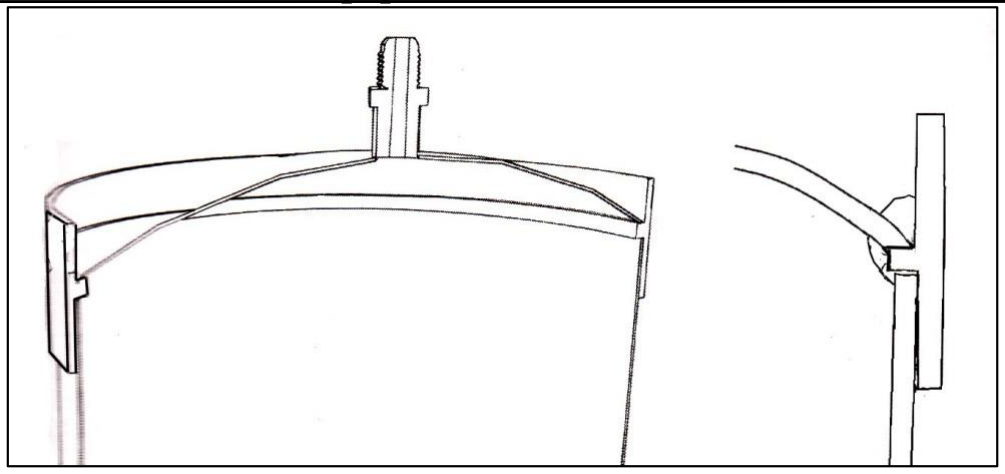
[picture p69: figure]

Technical papers

Author: Rick Newlands | 15 | updated: 06/11/16

Composite tanks
Several decades ago, space and aerospace companies identified the need for low mass pressure vessels. The composite overwrapped pressure vessel was developed to provide weight savings without a loss in safety margins over traditional tanks. The design consists of a thin liner of material, typically a metal, overwrapped with a continuous fibre yarn impregnated with a resin such as epoxy. The weight saving over a traditional tank is around 25 to 50 percent.

The general advice from composite manufacturers is that DIY home-made composite tanks have resulting properties that are far too variable from tank to tank to predict: use remote filling only.

More to the point, when composites are damaged or experience many pressurization-depressurisation cycles, the ensuing micro-cracks are rarely visible on the surface but will grow under mechanical stress, so the tank may rupture the next time it’s pressurized without any visible prior warning.

Even thin-wall aluminium liners are not thought to provide the whole structure with enough uniformity to allow anyone to be near one when pressurised.

One would hope, and industry demands, that the tank would leak before bursting, releasing the pressure. But this confidence only comes from very carefully controlled manufacturing, so that any cracks are known to be ‘stable’. Stable can be defined as a crack that has a length less than 10 times the wall thickness of the vessel, and has a stress intensity less than the material toughness (Ref. 1).

Don’t assume that a leaking liner makes the whole tank safe; a failed liner transfers more of the load to the composite, which can then undergo brittle failure. Make the composite strong enough to carry the entire pressure load.

If you treat your composite tank like eggs from the moment it’s made, then throw it away after its first flight then maybe…

But the whole point of all the hassle of a composite tank is to go for absolute minimum tank mass, so there’s absolutely no point in building a composite tank that isn’t remote-filled.

Composite tanks need a separate internal liner because raw composite leaks the contents inside through microcracks, and furthermore the resin can cause nitrous oxide to ‘explosively’ decompose, or form an explosive with Lox and probably HTP.

Plastic liners are lightweight, but you must ensure that the plastic is one that isn’t a fuel or catalyst: using a polythene liner for example turns the tank into a potential hybrid if blowback of chamber gasses upstream occurs! Use the fluoroplastics such as PTFE or FEP.

Composite tanks are very sensitive to impact: write an impact-mitigation work plan (no big spanners to be dropped onto the tank) and consider safety shields around the tank.

Technical papers

Author: Rick Newlands | 16 | updated: 06/11/16

Tank testing
No pressure-vessel, nomatter who or what company made it, is at all safe until it’s been pressure-tested.
Until somebody’s tested it, don’t use it.

If there’s no information stamped on its base, or if some rocketeer who you know is bad at recovery-systems sells you a scarred and pitted second-hand tank, regard it as dangerous until you’ve tested it.

Don’t even assume that a tank specifically sold for nitrous hybrids will take full nitrous pressure; some are only designed to take the lower pressure that you get with a permanently-open vent-hole system.

Remember to test the tanks to the safety-margin that they’ll need: at least 180 bar for any nitrous tanks you’ll ever be near.

Many carbon dioxide fire extinguisher bottles are tough enough even to transport nitrous around in, but beware second-hand ones: test them first.

A safer testing method
The only safe (safer) way to test a high-pressure system is hydraulically: never use compressed gas or you’re just making a gas-pressurised grenade again.

Buy a hydraulic hand-pump and some hydraulic jack-oil from an auto-store (such as Halfords or the like). Before pumping the tank up, make absolutely sure you’ve bled all the air out of the system (no bubbles) by separately filling the tank and pump completely full of oil before you connect them.

For safety, arrange to have at the very least a solid brick wall between you and the tank during testing, or preferably the corner of a building.

You don’t need to be able to see the tank anyway: any leaks will show up as a steady drop in pressure on the hand-pump’s pressure-gauge, their location revealed afterwards as a green stain on fresh newspaper.

And if the tank bursts, the loud splurt of a soggy explosion sounds exactly like an enormous aquajet going off.

Bits of burst tank won’t go very far under fluid pressure, because fluids can’t store energy in compression nearly so well as gasses, but jack-oil is impressively messy: the whole area gets slimed.

Make sure nobody else can wander into the danger area while you’re testing, and take extra precautions if you’re testing a large tank.

After testing is finished, thoroughly clean the inside of the tank because jack oil is a fuel. Cleaning procedures are covered in later chapters.

The proof test
You’re looking for proof that the tank won’t rupture; hydraulically test the tank to 1.3 or 1.5 times the highest pressure you ever expect the system to encounter. (The proof test isn’t a to-destruction test, so the safety factor is lower.)

Remote fill systems
Sadly, tanks that can safely withstand 3 times nitrous pressure can be too heavy for some vehicles. If this is the case, then you should resort to developing a safe remote-filling system.

Technical papers

Author: Rick Newlands | 17 | updated: 06/11/16

If nobody’s ever going to be near a tank while it’s pressurised, i.e. only remote filling and dumping throughout the whole life of the tank, then the safety-factor on burst can be 1.0001, or however lucky your rocket is feeling.

1.5 times the expected pressure is a reasonable remote-fill margin for a reusable tank, but pressurise the tank and plumbing a few times to this pressure before first flight to be sure.

Pre-launch and aborts
Remote-fill systems must be designed to fail-safe, i.e. will empty the run-tank if electrical or pneumatic/hydraulic power is lost.

Otherwise, excepting a sniper, there’s no way to depressurise a remote-fill tank if the remote-fill system dies and the hybrid didn’t launch. You can’t approach the pad without serious risk to yourself, so the pad could be out of bounds until the Lox or peroxide has all evaporated, or the nitrous pressure lowers the following winter!

The simplest approach for nitrous hybrids is the one commonly used; the vent-hole’s secondary function is a deliberate leak to slowly lower the tank pressure in the event of an abort.

A deliberate leak is a good idea even on a vent-free system, and the time it takes to depressurize the nitrous tank is entirely up to you. (Evacuate the pad for an hour though, and the Range Safety Officer may become displeased!)

Below 20 Bar as read on a pressure-gauge through binoculars, gives the required safety factor of 3 again on the original 60 Bar nitrous pressure, and you can then approach the pad.

For safety, vent all remaining nitrous in an aborted fill, and wait 15 minutes before re-filling otherwise the tank will be excessively cold and thrust will be lost (see our physics of nitrous oxide article).

For Lox or peroxide systems externally pressurized by nitrogen or helium, a tiny leak at the top of the run tank still works as a means to slowly depressurize the tank gas.

Launch
The remote-filling mechanism absolutely must disconnect from the rocket at or before launch, otherwise half the pad gets carried aloft and the rocket vehicle crashes. Following the advice of NASA literature on remote disconnection systems, consider backup mechanisms incase the primary disconnection mechanism jams.

Too many backups decrease reliability (the KISS principle) but one backup increases reliability greatly.

For example, if the tie-down strap on the commercial Hypertech system breaks or wasn’t installed properly, then the backup is that the fill-line burns through almost instantly, before the rocket has left the pad.

The Reaction Research Society has launched rockets using an ingenious re-rig of a standard hydraulic quick-disconnect coupling: The coupling’s release-collar is tied to a stake in the ground, and the male part is fixed into the rocket pointing aft.

When the rocket pulls upward on the coupling at launch, the lanyard tied to the release-collar goes taut and the coupling disconnects automatically.

This is a good design for the backup release, which Aspire have adopted as ADV2b’s backup disconnect.

Technical papers

Author: Rick Newlands | 18 | updated: 06/11/16

Note that some quick-release couplings can’t be disconnected before de-pressurising the line.

Hydraulic overpressure, the head space
Pick up any fresh bottle of camping-gas or CO2 and give it a gentle shake; the sound of waves sloshing inside reveals that the bottle hasn’t been completely filled with liquid, there’s obviously a small amount of gas in there as well.

This small ‘head space’ or ‘ullage’ of gas is in there for a purpose, because after filling, the liquid’s density will change with any future changes in temperature. Infact just-subcritical fluids like nitrous, carbon dioxide, or butane, can change density rather a lot with temperature if they’re around room temperature. Similarly, Lox will change density as it warms.

The danger is that if the temperature increases, the liquid density will drop (see our physics of nitrous oxide article).

If the tank was completely full of liquid, then the tank’s fixed volume now won’t be enough to contain the mass of liquid as it expands. (i.e. increases its volume) If the tank is stoppered, the liquid will then self-pressurise. Liquids don’t compress easily, so the ensuing hydraulic self-pressure can often be enough to burst the tank, or any closed-off feed plumbing downstream of the tank.

To prevent such an accidental hydraulic overpressure, then just as in nature’s design of the egg, a small percentage of the tank volume is deliberately left free of liquid to allow for expansion with temperature. This gas pocket can then compress to absorb reasonable volume changes without overpressuring the tank.

(Seriously large run-tanks benefit from either a pressure relief-valve, which is a commercial safety valve designed to open at a set over-pressure, or a commercial burst-disc that is designed to burst at a set over-pressure.)

For nitrous, this ‘head space’ of gas is often created by situating a vent-pipe a little way below the top of the tank, so that the liquid never fills above the level of the vent (see our ‘The physics of nitrous oxide’ paper).

As every excess gram of run-tank matters, what is a reasonable minimum volume of head-space?
Using tables of nitrous properties with temperature (Ref. 2) the Aspirespace run-tanks are designed to absorb the liquid expansion caused by a 10 degree C increase in nitrous temperature after the vent is closed at the nominally British climate’s 15 degrees C. This requires a 12% ullage (12% of the tank volume is vapour) which reduces to 0.7% at 25 degrees C.

In practice, we use 13% to 15% depending on how accurately we know the tank internal geometry.
(See our physics of nitrous oxide article for the required calculation.)

The hybrid engine plumbing
Rigid pipework and welded joints are preferred for integrity, but swaged joints are better for modification or replacement of parts: cutting a pipe and welding it again can introduce metal particles and other contamination into the pipework.

Threaded joints should be avoided with oxidizer system plumbing, as the threads are difficult to keep clean. Where threaded joints can’t be avoided, use PTFE tape to seal the thread, not sealing compound. Be careful not to let strands of PTFE come loose and fall into the pipework as they can block injector orifices or jam valves.

Technical papers

Author: Rick Newlands | 19 | updated: 06/11/16

Be careful not to over-tighten stainless steel swaged fittings as they can ‘pick-up’ (cold-weld) i.e. jam solid.

Flexible hose should be used as little as possible and only where absolutely necessary, for example, where thermal contraction could occur.

Plumbing should be properly clamped and supported to minimise flexing, chafing, abrasion, resonance, and mechanical strain that could lead to the pipework breaking. The supports should allow thermal expansion or contraction where necessary. Rigid pipes should be supported as close as possible to each bend in the pipe.

Connectors and fittings that are to be disconnected during normal operation should be provided with tethered end-plates, caps, plugs, or covers to protect the plumbing from contamination or damage when not in use. Keep it clean!

Avoid rust coming into contact with nitrous vapour as it can act as a catalyst for the nitrous. This is particularly a problem with cheap zinc-passivated hydraulic fittings as their plating comes off or goes ‘chalky’ and the sulphide chemicals contaminating industrial-grade nitrous can rot them over time. Stick to stainless steel and aluminium fittings where possible.

Hybrid engines vibrate: use mechanical devices such as safety wire wrapping or bent metal tabs to prevent nuts unscrewing themselves.

When designing the plumbing, take note of high transient fluid pressures from pyrotechnic valves or other rapidly-opening valves that suddenly introduce high pressure fluid into a low-pressure pipe. The sudden ‘jolt’ can give pressures much higher than the pressure occurring once the system settles down.

To measure the tank and combustion chamber pressures you need to make a tiny hole in the tank and in the chamber. These holes (pressure-taps) are connected to very narrow pipes that lead to pressure sensors. Using only a small hole means that the flow won’t be disturbed much by the presence of the hole.

Make the narrow pipes about 30 centimetres long and running upwards with the sensor on top. Any longer and the gas trapped in the pipes won’t be able to react quickly enough to sudden changes in flow pressure, but any shorter and the hot combustion chamber gas could get all the way up the pipe and melt the sensor.

Proof-test and leak-test the plumbing.

Trapped gas/vapour will tend to collect in the highest points of the plumbing. Consider a valve there to bleed this off as with your radiators at home.

Right way up!
When you test your nitrous hybrid, it’s important to remember to mount the nitrous run tank so that it’s upright, as it will be in flight. The outlet of the tank must be at the bottom so that liquid nitrous comes out first and not vapour. Though this may seem obvious, it has been known for a static firing attempt to get this wrong.

The combustion chamber
As well as having suitable internal thermal insulation (such as Tufnol phenolic composite) the combustion chamber must not leak otherwise a plume of hot, escaping gas will erode the leak far wider and cause a burn-through, so leak-test the chamber by plugging the nozzle. Viton rubber O-rings are sufficient to prevent leaks in nitrous engines, but they melt at lowish temperature so should be shielded from the hot chamber gas by a covering of insulation (this traps a pocket of cool air which protects the O-ring). For Lox engines, use copper gaskets.

Of course, the chamber is also a pressure vessel so needs to be hydro-tested as was done with the tanks (see earlier).

Technical papers

Author: Rick Newlands | 20 | updated: 06/11/16

Nitrous leaks
Leaks show up in any pipe-joints carrying the liquid phase of nitrous as regions covered in ice; the nitrous sucks heat out of the atmosphere as it leaks out to atmospheric pressure and vaporises (see our physics of nitrous oxide article), freezing the water-vapour in the air around the leak. It’ll freeze your hands or face too if they’re near a leak: wear goggles and gloves when you work with nitrous.

Cryopumping (sort of)
As the first syllable suggests, this pitfall should only occur at cryogenic temperatures such as when you use Lox, but it caused the demise of our first nitrous hybrid Rickrock flight (ADV2c), so is worth mentioning.

Rickrock 1’s manual-fill system used a manual vent-valve, this was a simple banjo-bolt that was screwed shut after filling. On this occasion, we didn’t realise that it had frozen partly open due to a phenomenon akin to cryopumping up the threads of the bolt during a pause in the filling operation. This caused a leak that slowly lowered the run-tank pressure, and Rickrock 1 sailed away on a low, flat trajectory that broke the recovery system due to too high an apogee airspeed.

Cryopumping occurs when the metal of some cavity is chilled by cold fluid in contact with it. The cold reduces the local pressure, and reduces the volume taken up by (increases the density), of the air in the cavity, and so more air flows into the cavity from outside.

Despite any previous purging of the cavity by inert gas, this air flowing in from outside contains water-vapour, which freezes on contact with the cold wall.

Although the term cryopumping implies cryogenic temperatures, vapourising nitrous will also chill metal components sufficiently for this to occur.

We’ve since redesigned the vent-valve for Rickrock 2.

Reverse flow
This is thought to be the main hazard to hybrids, the most likely hazard to occur:

Terminal flatulence
We all want the highest combustion chamber pressure to get the biggest specific impulse; as close to the tank pressure as possible, but there’s a practical limit.

A common trend is to use too large a hole/holes for the injector, in order to minimise the pressure-drop across it, but this is a very dangerous practice.

The pressure drop is there partly to prevent very hot combustion chamber gasses having the potential to flow back upstream into the feed system or tank if there is a chamber pressure pulse. Too low a pressure drop across the injector encourages such audible forward-reverse flow oscillations in the chamber:
Screaming hybrids are NOT cool, they’re dangerous: hot gasses could get back into the feed system and start a fire (or decompose the nitrous there in a nitrous hybrid).

Use a smaller orifice size to get the chamber oscillations under control.

Ref. 3, in line with most injector design practices, advises a pressure drop across the injector of 20 percent of the combustion chamber pressure at the end of the liquid phase of the burn when the tank pressure is at its lowest.

On a particularly cold day in the UK (i.e. a low tank pressure), a commercial nitrous hybrid with too large an injector orifice (causing too low an injector pressure drop) went boom. The Space Propulsion Group have had several nitrous hybrid feed pipe explosions while still with liquid in the tank, believed to be caused by reverse flow into the feed system.

Technical papers

Author: Rick Newlands | 21 | updated: 06/11/16

For example, at the end of the burn, our Aspirespace nitrous tanks are at about 36 Bar, so we tune the nozzle throat size so that the chamber pressure is no higher than 30 Bar at the end of the burn as 30 Bar times (100+20) percent = 36 Bar
The injector pressure drop therefore has to be 36 – 30 = 6 Bar

To re-iterate, make sure that the upstream feed pipe (between run tank and injector) is suitably wide enough (large enough cross-sectional area Apipe) that the flow velocity within it is less than 10 metres/second (Ref.3, i.e. effectively stagnant) to minimise pressure losses in this pipe, otherwise you’ll get an unwanted pressure drop along the pipe which reduces the injector pressure drop.

Then use the following equation to design the number of orifices required by the injector:

n =

ṁ oxidizer

Aorifice √
K

2 ρoxidizer ∆P

(from the continuity equation inserted into Bernoulii’s equation)

Where n is the number of orifices, ṁ oxidizer is the oxidiser mass flow rate in kg/sec, Aorifice is the internal cross-sectional area of one orifice (metres²
), ρ is the liquid oxidiser density, and ΔP
is the required injector pressure drop (Pascals) at the end of the burn.

We've experimentally determined the energy loss (head loss) constant K for nitrous oxide to be approximately 2.0 as the nitrous partially vaporises within a sharp-edged injector orifice giving a froth of 2-phase flow. (Length of the orifice divided by its diameter was around 4). For Lox or peroxide use a K value from the internet.

Another way to blow up the feed system is to let hot igniter gas back-flow through the injector. Don’t let this happen.

Technical papers

Author: Rick Newlands | 22 | updated: 06/11/16

### Part 3: Nitrous oxide decomposition hazards

The day the hybrid world changed
On the 26th July 2007 a terrible accident occurred at Scaled Composites’ hybrid test site in the USA. Three of our fellow hybrid rocketeers died when a very large flight-weight run tank of nitrous exploded, and they were all way too close to the tank wearing only tee-shirts and no facemasks when it happened.

This accident sent shockwaves around the world; many amateur rocketry groups became scared of nitrous and either halted their research or switched to a different oxidiser.

After the accident, research and evidence was uncovered which showed that nitrous has a dark side to its nature that we were unaware of. A lot of this research was done years before the Scaled explosion; it would have been nice if those researchers and ‘professional’ rocketeers could have been bothered to pass on their findings to Scaled and to us before the accident.

But I think the world has over-reacted to the Scaled accident. Now that we have more knowledge of nitrous we simply have to incorporate the new findings into our hybrid designs. There’s no need to demonise nitrous; it’s still one of the safest rocketry oxidisers.

What happened?
So what exactly happened at Scaled?
The complete answer may never be known for sure because Scaled - unhelpfully - have refused to release details. But two theories have emerged as information trickles out of Mojave with time.

The facts are that a large composite run tank had been filled with nitrous in preparation for a flow test of the hybrid injector. This test was cold: there was to be no ignition of the motor, however, some sort of electromechanical device, the Case/Throat/Nozzle (CTN) simulator was added to the downstream end of the injector to simulate the pressure of a combustion chamber. The engine design had the injector integral with the downstream wall of the nitrous tank.

During the flow test, the CTN simulator reacted with the nitrous flowing through it and exploded. This fired the injector rearwards into the composite tank which shattered. With the loss of the injector, a flame front would have travelled back into the tank.

The majority of the nitrous spontaneously decomposed into nitrogen and oxygen gas, with a large release of heat from the decomposition (the casualties suffered severe burns though it was shrapnel from the tank that killed them) that raised the run tank pressure. This overpressurised the run tank, and as there were no pressure relief devices on the tank such as a burst disc or pressure relief valve, the tank burst.

Although a lot of damage then occurred to the test area, it was significantly less damage than would have occurred had there been a detonation of the nitrous. The definition of a detonation is that the flame front spreads through the nitrous at supersonic speed. In fact no evidence has yet been uncovered to suggest that nitrous will detonate.

The data suggests that spontaneous decomposition can occur, spreading through the nitrous at a rapid pace, but significantly slower than a typical fuel-air deflagration. It appears that only the nitrous vapour is the culprit, liquid nitrous doesn’t appear to support continued decomposition because the surrounding liquid soaks the heat out of the reaction (this is called quenching): all attempts in the literature to ignite liquid nitrous have failed.

It’s probable that the damage at Scaled was caused by a BLEVE event. This stands for Boiling Liquid Expanding Vapour Explosion.

Technical papers

Author: Rick Newlands | 23 | updated: 06/11/16

When the nitrous vapour decomposed and, along with the injector, ruptured the tank, the tank pressure suddenly dropped to the pressure of the atmosphere outside the tank. This caused all of the liquid nitrous to flash-boil into vapour, expanding enormously in the process.

This expansion provided the energy for propagation of further cracks in the tank wall (shrapnelling) and then propulsion of these fragments of tank at very high velocity.

The expansion was further enhanced by a greater number of moles in the decomposed gasses and their increased compressibility factor (a so-called ‘real’ gas effect).

As this was happening, the now greatly increased amount of nitrous vapour decomposed, causing a release of heat which caused further gas expansion.

Complete decomposition of the nitrous in a run tank will theoretically cause a 20 times increase in pressure, though the tank will have burst long before reaching that pressure. [Note: Pressure relief valves are sized to release pressure fast enough to prevent the pressure from increasing beyond the strength of the vessel, but, for nitrous, not so fast as to be the cause of an explosion. An appropriately sized relief valve will allow the liquid inside to boil slowly, maintaining a constant pressure in the vessel until all the liquid has boiled and the vessel empties. Basically, too large a relief valve orifice or burst diaphragm could cause a BLEVE event.]

Alternatively, the Knights Arrow team (Ref. 4) note that every indication suggests that the tank was filled hours earlier then left to the mercy of the desert heat: the test was then run at the hottest part of the day.The ambient temperature was reported as 40+ degrees C. If the ambient temperature (in the shade) was 43 degrees C, the temperature a few feet above the concrete pad would probably have been in excess of 60 degrees C!

Nitrous goes supercritical at 36 degrees C (see our ‘The physics of nitrous oxide’ paper) so the tank or plumbing could've contained supercritical nitrous. Supercritical nitrous is very susceptible to pressure-shock which will result in a very high velocity decomposition during which temperatures can exceed 3,000 degrees C. This may have caused the demise of the MARS team’s Deimos Odyssey nitrous hybrid in the heat of the Blackrock desert USA.

The key question is, what caused the nitrous vapour to decompose?

It turns out that nitrous is a good solvent, particularly if it’s supercritical. The Scaled run tank used a composite tank liner, so bare composite resin was in contact with the nitrous, as well as the waxy deposits that you get on the surface of composites. Nitrous can dissolve the hydrocarbon binders in the resin. This became the fuel, or possibly the catalyst, for the decomposition. Plastic saturated with nitrous can decompose ‘explosively’ when ignition energy is provided.

Static discharge
What provided the ignition energy?

It was a hot, very dry day in the desert test area that day, which is conducive to the build-up of static electricity. Our nitrous hybrids typically have metal tanks and combustion chambers, so they’re earthed when in contact with our metal test-stands. But the Scaled hybrid had a composite tank and chamber. Assuming that the injector plate was metal, then this could have built up a large static charge as the nitrous flowed through it. The electrical conductivity of nitrous is low enough that with flowing nitrous it is theoretically possible to produce a large enough static discharge to initiate decomposition.

As liquid nitrous flows through an injector, nitrous vapour appears. This vapour can be easily ignited by an electric spark at typical tank pressures, and even a very feeble spark will do it (0.14 joule).

Technical papers

Author: Rick Newlands | 24 | updated: 06/11/16

One rocketeer from Arocket recounts: “I can tell you from personal experience that a big spark will set off nitrous.”

CTN
The other candidate for ignition was the Case Throat Nozzle (CTN) simulator device itself. It appears to have exploded, perhaps oil or grease plus electricity reacting with supercritical nitrous.

Scale effect
Another issue with the Scaled (sic) hybrid was its large size; probably the largest nitrous hybrid ever tested.

As hybrids get larger, the decomposition hazard increases with increasing system scale due to tank wall surface-to-internal volume scaling: there’s simply more mass of nitrous per wall of tank.

And there’s the quenching effect: the radius of the feed pipes of many of our small amateur hybrids are smaller than the quenching distance. This is a size (around 7 mm for pressurised nitrous, though it changes with pressure) below which the metal walls of the pipe are near enough to soak up any rogue heat energy from decomposition, stopping the reaction dead.

In Ref. 9, the researchers could only get nitrous vapour to sustain a reaction in a ½ inch diameter (12.7 millimetre diameter) metal pipe by heating it prior to ignition (204 degrees C and 55 Bar). In a 1-inch pipe and larger, there was no quenching at typical nitrous pressures.

Rocketry use of nitrous
Nitrous has many uses, from medical anaesthetic to dispensing whipped cream, and it’s been used for over 100 years. There have been very few accidents. (Excepting the poor souls whose colons exploded during surgery due to catalytic decomposition of nitrous anaesthetic reacting with intestinal chemicals. Farted out of existence is a sad way to go…)

But the rocketry use of nitrous is a new thing, we’re still in the learning phase:
- Rocket propulsion is unique in that large quantities of nitrous are stored at room temperature in thin-walled flight-weight tanks.
- The combustion chamber is closely coupled to the run tank. This is a significant source for ignition which does not exist in other applications.
- Nitrous oxide can be safely handled in extreme conditions in the liquid state, but hazards exist in the vapour state or supercritical state at elevated temperatures and/or pressures.
- The release of thermal energy is by exothermic molecular decomposition; this has a handy side-effect in that it helps motor combustion stability.
- There is a large energy release upon decomposition, about double that produced by an equivalent weight of TNT.
- Despite its potential decomposition hazard, if handled properly, nitrous is one of the safest rocketry oxidisers.

To minimise the risk of decomposition, SpaceDev stores its nitrous in liquid form at –18 degrees C (zero degrees F).

Let’s look at the hazards:

Contamination and degreasing
The presence of even a small amount of fuel or catalyst material in tanks and feed plumbing can greatly reduce the energy threshold required for initiation of nitrous decomposition. A mixture of nitrous and 9% hydrocarbon (ethanol) initially at only 40 degrees C exploded in a lab.

Technical papers

Author: Rick Newlands | 25 | updated: 06/11/16

I’ve listed compatible and non-compatible materials at the end of this chapter, though an awful lot of materials have still to be tested: if you google on nitrous material compatibility you’ll find that most of the websites are way behind the current research.

The way to deal with contamination issues is to give the system a damn good clean; equipment must be thoroughly degreased before use.

Degreasing

Professional rocketeers working on manned nitrous hybrid systems have, in my view, gone completely overboard on their cleaning since the Scaled accident. They’re using the strict procedures used for oxygen rocket systems. If you’re going to all the bother of full oxygen cleanliness, you might as well use liquid oxygen (Lox) in your hybrid as it’ll give you a much higher specific impulse.

Here’s one of their 4-step cleaning procedures:
- Dust and loose contaminants are removed by scrubbing, then the piece of plumbing is cleaned with oxygen cleaner, then rinsed in water.
- Ultrasonic cleaning of the part.
- Rinse and soak in de-ionised water 3 times to remove the oxygen cleaning agent.
- Dry the parts with nitrogen.
- Inspect cleaned parts, re-clean if they fail:
- Visual inspection looking for loose contaminants or grease.
- Wipe with a white lint-free cloth (check that the cloth remains clean).
- Ultraviolet lamp inspection.
- Store all cleaned parts in sealed plastic bags and re-inspect just prior to assembly.

For nitrous systems, industry uses the following, which Aspire recommends:

Clean parts in Isopropyl alcohol (in an ultrasonic tank if possible) then blow out the remaining Isopropyl alcohol with clean compressed air (not from an oil-lubricated air-compressor) or nitrogen, or wipe off with clean lint-free tissues/wipes.

For parts with inaccessible internal areas, put the part under vacuum or in a warm oven to ensure all the Isopropyl alcohol evaporates.

You can use Amberclene FE10 or aqueous alkali-based degreasers too. Or one can use dilute (20%) hydrogen peroxide to remove traces of grease from oxidiser tanks where it isn't possible to physically wipe the surface. This should only be done once any bulk contamination has been dealt with or it’ll ignite!

If you budget won’t permit the above, hybrid parts can be degreased using domestic cleaning products (detergents) in water, automotive brake-part cleaner, or preferably Isopropyl alcohol, then dried in a warm oven for a few hours.

If degreasing elastomeric seals (e.g. O-rings, washers) then check material compatibility first and don't leave them soaking in solvents for long periods as they can swell-up/soak up the solvent. Instead, rinse for a few seconds then wipe dry.

The use of Isopropyl alcohol (and other organic solvents) has safety implications: it has a flammable vapour which is heavier than air but the vapour pressure is quite low so explosion risk is rarely an issue, but don't use it near sources of ignition (including electrical contacts like switches, thermostats, or relays.) Don't inhale the vapour, and use in a well ventilated area. Also, it is mildly toxic when absorbed through the skin, so wear plastic gloves.

Bear in mind that thousands of grubby HPR nitrous hybrids get assembled in muddy fields and lobbed skyward generally without incident, though their small size might be saving them (quenching distance).

Technical papers

Author: Rick Newlands | 26 | updated: 06/11/16

Incompatible grease
Although a properly installed O-ring in a properly designed groove will seal perfectly when dry, it’s become an amateur and HPR rocketry habit to smear some grease around the O-ring, primarily to give a sacrificial heat-proof coating.

There have been several instances of people reaching for their solid rocketry supply of petroleum jelly/vaseline and smearing nitrous hybrid engine O-rings with it.
A little thought reveals that such grease is a fuel, whilst the nitrous is an oxidiser: sure enough their hybrids blew up upon ignition.
Use only oxidiser-compatible lubricants: these fluorocarbon lubricants can be bought from SCUBA diving suppliers or rocketry vendors.

Adiabatic compression
This is also called ‘water hammer’ (even though there’s no water), and until recently we all thought it only occurred with pure high-pressure oxygen (Gox). Aspirespace had to design against it for our H20 Lox hybrid.

What happens is that if a run valve is opened suddenly, Gox rushes down the feed pipe until it hits another shut valve or obstruction such as the injector. The Gox's momentum piles it up against the shut valve, and the temperature rises purely because of the compression. This self-heating can reach the ignition temperature of the pipework, and start a fire.
In nitrous' case, the self-heating can reach its auto-decomposition temperature.

Here’s a note from XCOR: “We had a few milligrams of fuel in a Snaptite valve which we didn't know about; we had some nitrous in it as well, and we hit it with a water
hammer. Adiabatic heating made the fuel/nitrous mix diesel, and that was enough, in that small space, to set off the nitrous. The result was a very loud CRACK! and a thoroughly ruined Snaptite valve.”

The way to prevent adiabatic compression is to avoid sudden rushes of oxidiser: open run valves slowly and reduce the dead-space downstream of valves: dead volumes in the feed lines (e.g. a tee fitting) are prone to adiabatic compression. Reduce the pressurisation rate of your run-tank as you fill it to no more than 20 psi per second (Ref. 11) to avoid adiabatic compression. The way to do this is to reduce the diameter of both your fill pipe and your run tank vent.

Bruno Berger at the Swiss Propulsion Laboratory (Ref. 13) understandably worries about imploding cavitation bubbles of nitrous vapour, because when they implode, they can generate very high temperatures.

As the liquid nitrous flows down the feed pipe between tank and injector its pressure drops, which causes some of the liquid to flash into vapour (2-phase flow) causing lots of little vapour bubbles.

If you get an adiabatic compression in the feed line or at the injector, these bubbles could implode. If there are enough of them imploding then the froth could generate decomposition energy faster than the liquid nitrous can quench it, leading to the feed pipe overpressurising (blows up).

The way to minimise 2-phase flow is to follow the advice of Ref. 3 which recommends keeping the pipework wide enough to keep the liquid nitrous flow-speed V below 10 metres per second, because the drop in pressure of the nitrous as it flows through a pipe varies with V²
(Bernoulii’s equation).

Use the mass continuity equation:

Technical papers

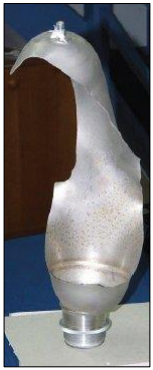
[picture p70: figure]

Author: Rick Newlands | 27 | updated: 06/11/16

V =

ṁ
ρA

where ṁ is the mass flow rate of nitrous in kg/sec, and A is the cross-sectional area of the pipe in metres²

. Use a nitrous density ρ of 744 kg/m³ (a hot day)

Keeping the flowspeed low similarly avoids pressure changes due to sudden changes in pipe cross-section (particularly at valves) which can trap a pocket of vapour. Avoid changes in cross-section.

The Knights Arrow team avoid nitrous vapour entirely by pressurising their liquid nitrous run tank using a nitrogen-powered piston. This raises the nitrous way above its vapour-pressure so that vapour cannot form. Personally, I think this is over-kill, but as it’s a manned hybrid, it’s their call.

Reverse flow: Flashback through nitrous vapour
Flashback of hot chamber gasses into the nitrous vapour after all the liquid has run out is thought to be a greater hazard (Ref.11) than before the liquid runs out. This is because there’s much more vapour in the feed system, and this vapour goes all the way up and into the tank, so the tank can go boom too.

Hybrids have exploded when the liquid nitrous has run out, and a chamber pressure spike has reversed the flow.

Here’s a picture of the remains of a run tank (thanks to Troy from Arocket) after a flashback event at the end of a run resulted in an explosion of the vapour within the tank:

Inadvertent liquid engine, a hard start:
One of the biggest bangs of recent years in the U.K. professional (defined as getting paid for it) rocketry field occurred when a nitrous hybrid engine accidently became a liquid engine, and then blew up.

The nitrous must not be in liquid form once it’s inside the
combustion-chamber because of the danger of it pooling in corners
of the motor; molten plastic fuel may be pooling in the same corner.

In this case, the nitrous was injected tangentially into the chamber instead of axially for several promising technical reasons, but centrifugal effects re-compressed the nitrous, and at the higher pressure it reverted into a liquid again. A design oversight allowed molten plastic to occupy the same area, and it did the classic liquid rocket engine ‘hard start’ upon ignition.

This bang was compounded by the fact that the feeble igniter was situated at the nozzle instead of where you ought to put it: close to the injector, so the chamber could happily fill with unburnt nitrous.

Technical papers

Author: Rick Newlands | 28 | updated: 06/11/16

One way to fill the chamber with liquid is to use too large an injector orifice, with its resultant too low a pressure drop. This could keep the nitrous from vaporising properly.

Arocket have seen “a very scary explosion of a thin-walled steel nitrous oxide tank due to a hard start with a paraffin hybrid. When the pyro (run) valve failed, a much larger volume of nitrous entered the preheated, flame-filled combustion chamber, and decomposed. Bits of combustion chamber went everywhere; we never found the injector.”

Pacific Rocket Society, Black rock desert, November 1995: a fill line leaked inside the combustion chamber, saturating the HTPB fuel with nitrous. Upon ignition the chamber blew up.

Warming the run tank
On cold days, the run tank has to be heated in order to get the nitrous pressure up (see our ‘physics of nitrous oxide’ paper). It goes without saying that care has to be taken to avoid hot-spots that could decompose the nitrous. If you’re using an electrical tank heater, don’t let it overheat.

Hot-spots within heat exchangers have been found to set off nitrous: use a heat exchanger coil with a uniform wall temperature such as a coil submerged in a water bath to warm nitrous.

Now that we know the hazards, what can be done about them?

The decomposition process
Know thine enemy: it’s instructive to review the decomposition process. See Ref. 11 for a very detailed theoretical model, the results of which are summarised below:

Nitrous decomposition is a marginal reaction with just enough heat released to sustain itself. It is easily quenched: either nearby metal pipe walls or a dilutent gas added to the vapour act to absorb heat and quench the reaction.

The decomposition rate of nitrous vapour is 6 orders of magnitude slower than peroxide decomposition, making it a safer oxidiser: it’s less sensitive. This abnormally low reaction rate is partly caused by “the non-adiabatic spin-forbidden transition elementary unimolecular decomposition process” (it’s a quantum thing: I don’t understand a word of it either!)

All attempts in the literature to ignite liquid nitrous have failed (unlike liquid peroxide).

Small concentrations of dilutent gas added to the nitrous vapour increase the ignition energy of the vapour, making the mixture extremely difficult to ignite at dilution levels greater than 30%. Adding extra gas to the run tank is sometimes called ‘supercharging’, and has the side effects of raising the tank pressure slightly, and reducing the tendency for 2-phase flow in the feed system.

Reference 11 defines two distinct modes of nitrous decomposition:

Local thermal ignition
This is regarded as the most common mode/ greatest hazard expected in nitrous rocketry, since it requires only small localised quantities of thermal energy. This starts a self-sustained deflagration wave in the nitrous vapour (starting at the injector, once all the liquid has run out) that travels up the tank, causing havoc (decomposing the rest of the nitrous vapour).

The rate of increase of tank pressure (the violence of the explosion) that this causes depends upon this wave’s flame speed. The inherently slow decomposition of nitrous results in a low

Technical papers

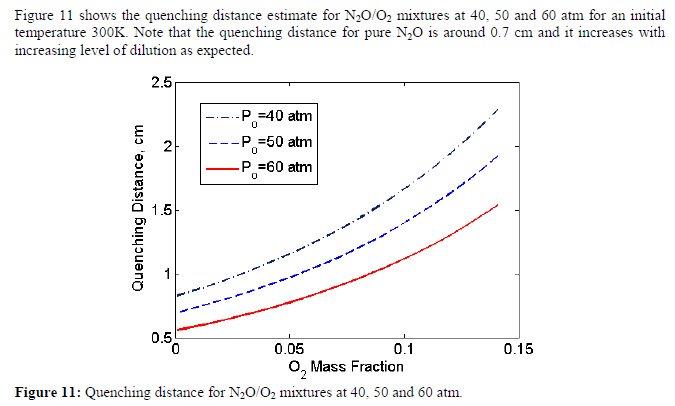
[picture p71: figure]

Author: Rick Newlands | 29 | updated: 06/11/16

flame speed of only 15 cm/second at 41 Bar. The flame speed decreases with increasing pressure and increasing dilution of the vapour.

The quenching distance (the maximum radius of conductive metal pipe that will quench the reaction) is around 7 mm for pure nitrous at 27 degrees C (300 K), and increases with dilution with inert gasses:

From a ‘point’ source or hotspot, the minimum ignition energy for pure nitrous vapour is very roughly 100 millijoules (not a lot). There is a big effect on local thermal ignition if you dilute the tank vapour: dilution by 30% Gox raises the ignition energy to roughly 500 Joules, making ignition virtually impossible.
(Note: as yet I’m not sure whether this dilution figure is based upon the mass of vapour at the end of the burn, or is based on the total nitrous mass at the start of the burn: I’m waiting to hear from the Space Propulsion Group.)

It may seem odd that adding Gox (gaseous oxygen) to the run tank actually makes things safer. I assume it adds a bit to the specific impulse as well.

Dilution with nitrogen is expected to have a similar effect, and helium is expected to be better: have the same effect at lower dilutions because heat gets conducted away more easily in helium. Ref. 10 suggests you need 4 times less helium compared to nitrogen.

The time taken for local thermal ignition-caused decomposition of the tank vapour to occur is surprisingly slow: a typical time to maximum overpressure is 5 seconds, (time to typical flight-weight tank burst is 2 seconds). This is slow enough for an automatic safety system to react and do something. Dilution doesn’t really change the maximum overpressure.

Technical papers

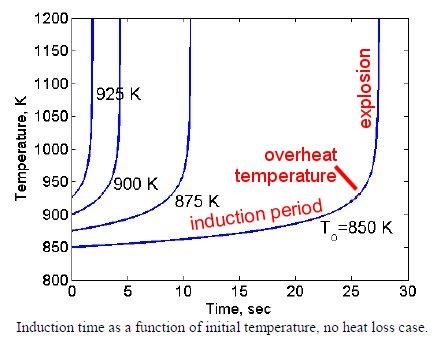
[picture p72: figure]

Author: Rick Newlands | 30 | updated: 06/11/16

Homogenous ignition
This is simultaneous ignition of a sizable bulk of the nitrous vapour when sufficient energy is added (high temperature, such as caused by a fire). It’s regarded as the less likely of the two types.

Above a certain high
temperature, the heat produced by the exothermic
decomposition reaction exceeds the heat loss to the
surroundings and the
temperature rises.

A slow increase in temperature
begins (an induction period).

This is followed by an exponential growth in temperature (causing very rapid gas expansion) once the temperature reaches the overheat temperature.

As this graph shows, below around 850 Kelvin, the induction period is too long for typical HPR propulsion systems (the nitrous has drained out of the tank and/or feed system by then) so auto-ignition is not going to happen.

Homogenous ignition is most likely to occur in the feed system due to reverse flow or adiabatic compression. It’s unlikely to occur in the run tank due to the need to heat the whole of the nitrous to its high ‘auto-ignition’ (short induction period) temperature.

The effect of diluting with inert gasses is small: even 80% dilution only raises the ‘autoignition’ (short induction period) temperature by 30 Kelvin.

Flame traps
There’s been talk on Arocket of the possibility of adding a flame trap to the feed line. (Technically it’s actually a quenching trap.)

Nitrous has a much larger quenching distance than typical fuel/air mixtures, so a grid of stainless steel tubes put streamwise into the feed line could be able to stop any decomposition that starts at the injector.

The quenching distance for nitrous is around 7 millimetres, so I reckon that a grid of 5 millimetre diameter tubes will work, and the tubes are large enough not to cause much of a pressure drop.

But I must stress that I haven’t found any evidence of anyone having tried a flame trap with nitrous. This is a (potentially hazardous) experiment that needs doing.

Nitrous material compatibility
Use stainless steel!

As a general guide, materials that are oxygen compatible are suitable for nitrous.
It’s worth pointing out that I haven’t seen any evidence for a catalyst for nitrous that works at room temperature, they all seem to need elevated temperatures.

Metals
Aluminium, Stainless Steel: satisfactory

Technical papers

Author: Rick Newlands | 31 | updated: 06/11/16

Copper and its oxides (and brass/bronze), nickel, and platinum, are highly catalytic with nitrous especially at elevated temperatures, so do not use these. Annoyingly this list includes the metals one would like to electroform into a thin-walled tank.

Carbon steels are corrosive in presence of moisture: do not use corrosion-prone metals because, for example, iron oxide (rust) is a catalyst. Avoid rust contamination from steel fill tanks; use stainless steel filters in the fill line to catch any rust particles.

Plastics
Fluoroplastics such as Polytetrafluoroethylene (PTFE), Polychlorotrifluoroethylene (PCTFE), Fluorinated ethylene propylene (FEP), Perfluoroalkoxy polymer resin (PFA), are satisfactory. Other plastics are an ignition hazard.

Nitrous can saturate plastics and composites turning them into ‘explosives’: HTPB fuel saturated with nitrous can be ‘explosive’.

Elastomers
Think carefully about what material to use as your run-tank O-rings. Just because commercial HPR hybrids use ‘rubber’ O-rings doesn’t automatically make it a good idea.

Fluorocarbon-coated O-rings (Buzak and Shamban catalogue): use these where possible. Unfortunately, they don’t stretch very much.

Buna-N and neoprene degrade in nitrous liquid after several days.
Butyl (isobutene - isoprene) rubber (IIR): not recommended, possible ignition and significant swelling.
Nitrile rubber (NBR): not recommended, possible ignition and significant swelling. Chloroprene (CR): not recommended, possible ignition and significant swelling. Chlorofluorocarbons (FKM) (VITON): not recommended, significant swelling.
Silicon (Q): satisfactory
Ethylene - Propylene (EPDM): not recommended, possible ignition and significant swelling. N.B. Silicone saturated with nitrous is an impact-sensitive explosive.

Lubricants
Nitrous can form an explosive with many hydrocarbons and lubricants:
Fluorocarbon based lubricant (krytox): satisfactory
Hydrocarbon based lubricant: definitely not recommended, possible ignition.

Recommendations
- Minimise the number of persons present in the test area whenever nitrous is being loaded/is loaded into the run tank or whenever nitrous is flowing.
- Avoid decanting nitrous in small, confined areas (or monitor air quality) as nitrous is an anaesthetic.
- Use a large-volume (large diameter) burst disc on the run tank. Mandatory for manned systems.
- For engine static testing, keep the run tank upright so only liquid gets to the injector at ignition.
- Keep it very clean: even very small traces of contaminating fuel can cause problems.
- Avoid the use of catalytic materials.
- Nitrous is a good solvent of hydrocarbons: grubby fingermarks, O-ring polymers, and valve seals.
- Venting the nitrous through the combustion chamber should be avoided at all costs.
- Dilution of the nitrous vapour in the run tank is recommended.
- Avoid hard starts: fire the igniter before admitting the nitrous into the chamber.
- If using nitrous in a confined space use an oxygen sensor to monitor dangerous concentrations of nitrous which could be inhaled.

Technical papers

Author: Rick Newlands | 32 | updated: 06/11/16
- Properly earth all ground support equipment (fill tanks and fill lines), and keep mobile phones and laptop Wi-fi switched off when anywhere near nitrous. Persons handling nitrous should preferably be earthed.
- Construct tanks and lines out of conductive material. For composites, work out a way of dissipating static (aircraft composites have metal foil as their outer layer to dissipate lightning strikes. Other approach is to embed carbon nanofibres or nanotubes within the resin.) Scaled are now using a metal tank internal liner.
- No part of the engine should have a resistance of more than one ohm between it and its adjacent parts so that potential differences (voltage) cannot build up. (Ref. 1)
- Avoid adiabatic compression: minimise feed-line dead volume downstream of the run valve, slow the valve opening.
- Prevent back-flow of igniter gas through the injector.
- Reduce the pressurisation rate of your run tank as you fill it to no more than 20 psi per second.
- Use small enough injector orifices and widen the nozzle throat to get a good pressure drop across the injector right through the burn (a drop of 20% of the combustion chamber pressure as the liquid runs out).
- Develop safety procedures, and pre-chill the pump, if you pump nitrous from the fill tank to the run tank.
- Use pressure relief valves/burst discs on all trapped volumes of liquid nitrous to prevent hydraulic overpressure.
- Review all moving parts in the nitrous system (regulators, valves) for friction, impact, and static discharge.
- Avoid eddies or stagnation zones in the feed pipework due to sudden changes in cross-section. These can act as flame-holders which prevent any decomposition from being flushed safely downstream.

Technical papers

Author: Rick Newlands | 33 | updated: 06/11/16

### Part 4: Liquid oxygen safety (Ref.s 1, 6, 17 – 21)

Lox Handling and safety issues
Liquid oxygen is a liquid with a slight bluish tinge to its transparency. It pours like water though is denser.

Oxygen is in fact one of the safer rocket oxidisers as it isn’t corrosive, but in its cryogenic liquid form it is of course extremely cold, so spilling/splashing it on bare skin will cause severe 'cold-burns’. Note that Lox does not wet the skin for exactly the same reasons that liquid nitrogen doesn't: vapour pressure (the Leidenfrost effect: a phenomenon in which a liquid, in near contact with a mass significantly hotter than the liquid's boiling point, produces an insulating vapour layer keeping that liquid from boiling rapidly.)

Oxygen is a powerful oxidiser in both gaseous (Gox) and liquid (Lox) states and its use involves a degree of risk that you should never overlook. Oxygen is reactive at ambient conditions, and its reactivity increases with increasing pressure, temperature, and concentration. Many materials that don’t burn in air will burn beautifully in oxygen-enriched atmospheres and will do so with lower ignition energies and faster burn rates than in air. Most non-metals are flammable in 100 percent Gox at ambient pressure (or Lox), and most metals are flammable in Gox at increased pressure or Lox.

Impressively destructive fires have occurred in every industry or venue in which oxygen enriched atmospheres are used.

Typically, a flow of Lox from a run tank through the rocket engine plumbing is preceded, and followed, by a flow of Gox, so review your plumbing for both Gox and Lox flow: both have their respective hazards.

Inhaling cold Gox at high concentration will severely damage your lungs: severe frostbite or actual ignition.

Infiltration
Gox, being a small diatomic molecule, has a habit of seeping into anything porous, such as foam insulation, clothing, or up trouser-legs.
It can also get trapped in people’s hair, and most hair cosmetics are utterly flammable. It is wise to avoid all hair products and makeup on firing days.

Anyone coming in contact with a fair concentration of Gox (accidently, or during filling of a run tank) must stand outdoors, preferably in a breeze, for at least 30 minutes (Ref. 18) to let the Gox dilute and dissipate from their person and clothing, and also from their skin. Waiting only 5 minutes for the Gox to dissipate then lighting a cigarette, or turning on the ignition of a car, or using a mobile 'phone or laptop Wi-fi, would all be extremely hazardous. And don’t use any tools either: can cause a spark.

If oxygen escapes into an enclosed space or building, open all the doors and windows. Do not connect electrical power or carry out any maintenance for at least one hour (Ref. 18) after this event, to allow a potential oxygen-enriched atmosphere in the building to dissipate.

If using Lox in a confined space/indoors, use an oxygen sensor to monitor dangerous concentrations of Gox which could be inhaled.

Clothing
Protective clothing, goggles and gloves, are mandatory for those involved in any handling of Lox. BOC sell suitable gloves and aprons at their supply depots. If there's any chance you might get sprayed with Lox or have to crawl through some in an emergency, dress accordingly.

Technical papers

Author: Rick Newlands | 34 | updated: 06/11/16

Gloves for use around Lox systems must have good insulating quality. They must be designed for quick removal in case Lox gets inside them. Because footwear may also get Lox inside, shoes must have high tops and trouser legs must be worn outside and over
the shoe tops. The trousers must have no external pocket openings and no cuffs. The shoes should be made of leather.

When you’re working with Lox, always wear natural fabrics (inside and out - no nylon underpants under your wool trousers) because plastic fabrics tend to melt and stick to the skin causing severe burns. If you spill Lox on your clothes, get them off as quickly as you can.

Several oxygen safety manuals, e.g. the one from NASA Lewis, say that clothing splashed with Lox or permeated with Gox can remain dangerously flammable for a surprisingly long time and should preferably be taken off at once.

Probably a better idea would be a safety shower. Hose down scrupulously, then take the clothes off while you are still under the shower. Clothing saturated with oxygen would turn you into a very good representation of a roman candle.

Do not wear shorts around Lox!

Shoes for shop work that one can get out of very quickly if need be are recommended.

XCOR have the same rule for synthetic fabrics around Lox. It's not absolutely prohibited, but it's strongly discouraged: it can't be the only layer, and if it's an outer layer, you need to be able to take it off in two seconds. People get the hint pretty quickly, and generally only wear natural fabrics to work.

When working with oxygen, clothing must not be worn that produces sparks or static electricity, such as nylon, orlon, dacron, wool, silk, or shoes with steel taps or hob nails.

Warm water
Water hoses should be available to thaw valves and fittings on cryogenic storage containers. Atmospheric moisture may freeze on valve stems and similar components, making them impossible to open or close. Running water onto the frozen part may thaw the ice and enable component operation. Running water is also useful to thaw ice if someone’s gloved hand freezes to a valve handle.

Explosive contamination
Liquid oxygen explosives use a cartridge of (usually) charcoal soaked in Lox. One charcoal brickette soaked in Lox has the explosive potential of a stick of 30% dynamite.
(Needless to say, don’t try this at home; it's friction, impact/shock, and static sensitive.)

Not as dangerous as a number of other materials, but a lot of stupid lab tricks with Lox and various organic materials can detonate in the hand rather than the floor they're thrown at... When it's well-mixed with Lox, almost any organic material is an explosive - the details don't matter very much.

Just about anything that will burn may explode if sensitized with Lox: wood, paper, clothes, shoes. The Reaction Research Society had a Lox/tarpaper hybrid explode quite spectacularly ("detonate"), and it was attributed to an unsuccessful previous ignition attempt leaving the tarpaper saturated with Lox.

Dust, lint, or fine metal particles (swarf) can also cause an explosion, so don’t do any filing, and only use lint-free cloths.

Lox and asphalt are a contact explosive. The rule is the obvious one, don't work with Lox on or over an asphalt surface. If you do spill Lox on asphalt, don't step in it! Apparently this happened at Edwards Airforce Base many years ago, and blew a guy's foot off.

Technical papers

Author: Rick Newlands | 35 | updated: 06/11/16

The Lox evaporates, but the asphalt is still saturated with oxygen. It can remain explosive and impact-sensitive for hours at moderate temperatures.

At the very least, Lox and asphalt are highly flammable (asphalt has been used as a fuel in some hybrids): a Lox spill at Cranfield University U.K. in the 60’s burnt-out half the car park.

If you spill Lox on asphalt, cone it off. If there is a chance of traffic in the area for the next several hours, post a guard.

To reiterate: when working with cryogenic fluid:
- Wear eye protection: goggles or face-shield.
- Wear the specified protective clothing: the gloves and apron.

When working with Liquid oxygen:
- Hair and clothing will absorb gaseous oxygen while working with Lox.
- It will take at least 30 minutes for this gaseous oxygen to dissipate once you’ve left the test site.
- Avoid potential ignition sources (naked flames, lighters, soldering irons, cars, electrical equipment) while handling Lox, and for at least 30 minutes afterwards.
- Avoid wearing flammable cosmetics. (e.g. hairspray, brill-cream, hair-gel)
- Wear only natural fibres, and not ones that create static.
- Remove oxygen-saturated clothing.
- Ban all smoking.
- Take care with mobile ‘phones: switch off all ‘phones at or near the test/filling site as they have the electromagnetic strength to cause sparks. Switch off laptop Wi-fi’s for the same reason.
- If oxygen escapes into a confined space, evacuate the building for one hour.
- Be aware that Lox mixed with organics can form an explosive.
- Do not use Lox over asphalt.
- Keep hands and tools free of dirt and grease: use degreased tools specifically nominated for use with the Lox plumbing only.
- Avoid the creation of dust, lint, or swarf around oxygen.

Team safety
Firing team member safety should be the paramount design driver for the rocket engine and its plumbing, and this is achieved mainly though remote actuation of the engine and its valves from a considerable distance.

Emergency operation
Be sure to hold several design reviews of the rocket engine’s plumbing in order to make sure it can cope with all potential emergency situations. Try to design-in fault tolerance.

There must be facility to quickly shut-down the engine and dump the contents of the Lox run tank well away from the test-stand. The outflows from both this drain/emergency dump valve, and the run tank burst diaphragm, should flow down a pre-purged pipe of considerable length to dump the Gox well away from the engine, into a pre-prepared pit where the Gox can dilute with the nitrogen in the air and dissipate. (Ref. 17)

Friction, impact, and static discharge
Review all moving parts in the Lox system (regulators, valves) for friction, impact, and static discharge, which could ignite the oxygen.

Dewars
Lox is supplied in a double-walled insulated metal tank similar in design to a vacuum flask, which is known as a Dewar tank.

Technical papers

Author: Rick Newlands | 36 | updated: 06/11/16

One person will have to manually connect and disconnect the Lox fill line filling the run tank from the Dewar, and one or more persons will then have to move the Dewar well away from the test firing stand. Choreograph these person’s actions and movements: ensure that they can carry out their allotted tasks in a safe manner.

Do not permit dirt, oil or grease to come in contact with the filling adapter on the oxygen cylinder or dewar. Oil or grease, even in minute quantities, may cause a violent explosion upon contact with oxygen.

Liquefaction
The air around uninsulated cryogenically cold metal pipes and tanks can become liquefied, separating into predominantly liquid nitrogen and liquid oxygen. This new Lox is a fire hazard. Insulate the tanks and pipework to prevent this. Liquefied air dripping onto asphalt or dirt/earth can ignite or form a contact explosive.

Oxygen fires
Oxygen fires cannot be put out.
Smothering the fire doesn't work, as the oxidiser remains in-situ.

You just have to let the fire burn out, though dilution of the oxygen may help.

In a Lox fire, the oxygen is typically boiling, and expanding by a factor of about 1000. This tends to blow the flames in every direction, whilst the oxidiser fans any secondary fires up really well.

Once an oxygen fire has started in the rocket engine plumbing, the metal plumbing can then catch fire and be completely consumed, leading to further fire and a major oxygen spill.

Sources of ignition (Ref.s 1, 18)
The following is a list of some potential ignition mechanisms for oxygen.
- Particle impact: minute particles of metal becoming entrained in a high-speed flow of Gox and then impacting some component of the plumbing. The energy of impact is sufficient to ignite certain metals such as aluminium and titanium. Limit flow velocities, and use filters to catch any stray particles. Items that can generate particulate contamination during operation include pumps, check valves, rotating stem valves, regulators, and quick disconnect fittings.
- Rapid pressurization (adiabatic compression: see later)
- Flow friction: The heat generated when oxygen at elevated pressures flows across or impinges on a polymer and produces erosion, friction, or vibration. Though poorly understood, this phenomenon can occur when maintenance or assembly damages the soft plastic of valve seats, leading to a leakage flow of oxygen across the seats. Using redundant seals can mitigate against this leakage.
- Mechanical impact: reactive metals such as aluminium, magnesium, titanium, and lithium based alloys as well as some lead-containing solders can be ignited by mechanical impact in the presence of oxygen, as can many non-metals. Regulators, relief valves, and check valves that chatter (oscillate rapidly exposing their polymer components to repeated impacts) can ignite the polymers. Dropping a metal tool on asphalt saturated with oxygen can cause a minor explosion.
- Friction: two or more usually metal components rubbing together: rotational or translational sliding contact, generates enough heat to ignite.
- Resonance: acoustic oscillations within resonant cavities causes a rapid temperature rise. A flow of high-speed Gox through a tee-piece of plumbing which has one leg of the tee closed can form a buzzing cavity. Keep the plumbing internally aerodynamically smooth to avoid areas of turbulence.
- Static electricity discharge.
- Lightning: provide lightning rods, aerial cable, and suitably connected ground rods in all areas.

Technical papers

Author: Rick Newlands | 37 | updated: 06/11/16
- Electrical arc: can occur from electric motor brushes, electrical power supplies, lighting, etc.
- External heat.
- Shockwaves and fragments from a ruptured tank.

Oxygen enrichment of the air due to a Gox spill greatly increases the hazards of flammable liquids, vapors and gases as follows:
- It widens the explosive limits. It does not affect the flash point significantly, so materials below the flash point remain safe. The increase is into the fuel rich area.
- It greatly reduces the energy required to produce ignition.
- It increases the rate of burning, and explosion relief becomes more difficult.
- Flame traps, flame-proofing of electrical equipment, etc. may become ineffective.

Another danger in the event of an upset is the mist explosion or torch effect when a mist or fine droplet spray of an organic liquid is discharged into an oxygen enriched atmosphere. Under these conditions an explosion can occur regardless of whether the organic liquid is above or below its flash point.

Oxygen enrichment can also render flammable some gases and vapours which are not flammable in air, for example ammonia and some halogenated organics.

Oxygen as it affects test-stand design (Ref. 17)
Note: for Lox test-site design, see the final chapter of reference 18.

Gox is heavier than air and pools on the ground, so a sloping test-chamber floor with guttering will encourage the Lox or Gox to flow away from the test-stand, in this case into a prepared pit to let it pool, dissipate, or burn itself out. Don’t let the oxygen enter drains, sewers, or streams. (You’ll blow-up the sewer, and then…) Nitrogen in the air will eventually dilute the Gox as it dissipates.

The outflow from the dump/drain valve, especially during an emergency dump, should flow down a pre-purged pipe of considerable length, and then out into a pre-prepared pit. The outflow pipe downstream of the burst diaphragm should also be connected to this long dump line. This keeps the Gox well away from the test area though if the wind direction would blow the Gox back again, no testing should be done.

The walls and floor of the test stand should be concrete, (not earth or asphalt) and should be scrubbed using only water before every firing session to remove organic and/or particulate material (dirt) which could be a fire hazard.

The brooms or brushes used for this scrubbing should be bought new at the start of the testing programme, and be clearly labelled so that they won’t accidently be used elsewhere with detergents (which are flammable).

Any cracks in the concrete tend to act as dirt traps, and should be filled-in.

The test-stand and all equipment must be earthed.

Technical papers

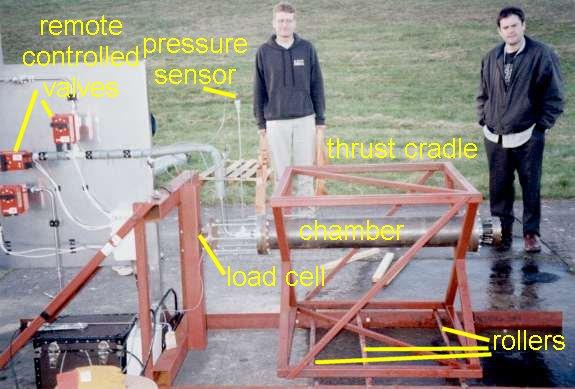
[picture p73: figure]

Author: Rick Newlands | 38 | updated: 06/11/16

Here’s Aspirespace’s test stand for our H20 liquid oxygen hybrid:

The rollers let the rocket move a little to butt up against the load cell, which is an electrical device that converts force into an electrical signal. This measures the thrust, and sends it down an electrical cable to be read by a computer.

Not shown in the picture above are heavy straps that hold the chamber and thrust cradle down to the ground, but let it move along the rollers a bit.

Plumbing design
Cryogenically-rated hardware is worth the expense, because you save all the hassles of making 200 year’s worth of cryogenic mistakes yourself. Not using cryo-rated hardware with Lox is like not using peroxide-compatible materials with peroxide. You'll probably get away with it, and it'll probably work most of the time. But it's not worth it, because the extra expense (damage/fire/explosion) when it doesn't work is higher than the savings when it does.

We recommend stainless steel pipework with Swagelock fittings. This allows disassembly for maintenance and modification.

Ball valves
Lox ball valves have to be vented; vented ball valves are a commercial off-the-shelf item. They’re more expensive, but they’re worth it.

The vent is there to release trapped Lox and/or trapped water-vapour: liquid water is the enemy in cryogenic valves, because it will freeze and the valve will stick. Trapped Lox will evaporate and build up pressurized Gox in the valve, where it will happily wait for an opportunity to ruin your day. So if you intend to close a standard ball valve full of Lox, drill and de-burr a hole from the high pressure side to the centre of the ball, otherwise expanding trapped Lox within the ball cavity may blow out the valve seal. This may not be necessary for the main run valve since it gets opened until all the Lox is gone.

The ball valve vent should have a short tube attached to it so that condensation won't occur on the ball or seal. Water at Lox temperatures is harder than steel.

Technical papers

Author: Rick Newlands | 39 | updated: 06/11/16

Avoid rotating valve stems and sealing configurations that require rotation on assembly. Rotating valve stems and seals can gall and generate particulates.

Poppet valves
High pressures and high flow rates can produce side loads and oscillations on the poppet seal; these can cause metal deterioration by fretting or galling. (Galling is the more severe condition, because it involves smearing and material transfer from one surface to another.)

Fretting and galling can cause several problems in oxygen systems. The valve poppet may seize, resulting in loss of function. The frictional heat of the fretting or galling may lead to ignition of the valve. The particles generated by the fretting or galling may cause malfunction or ignition of another component downstream.

Where possible, the valve poppet should be designed for symmetrical flow so no oscillatory side loads are created. The symmetrical flow centres the poppet in the bore and maintains design clearances between the poppet and bore surfaces.

Check valves
Bear in mind that check valves (one-way valves) have a minimum back-pressure below which they will either not actuate, or will ‘chatter’. Check the information that comes with the valve.

You should have a check valve on the run tank vent. For example, use a 1.5 psi cracking pressure ball check valve in teflon and stainless steel on the outlet (XCOR). This keeps the system nice and dry with the vent wide open, and means that the tank contains only oxygen (and possibly helium) after the first fill cycle. This is good for keeping everything dry and clean.

Welds and soldered joints
Welded, brazed, or silver-soldered joints are satisfactory for oxygen systems. Such joints, however, if left in the as-formed condition, may have slag or surfaces that can trap contaminants. Welds should be specified as ‘full penetration’ so that the contracting surfaces are joined to limit particulate entrapment.

Exposed weld surfaces should be ground to a smooth finish for ease of cleaning.

With brazed and soldered joints, special care must be taken to ensure surface cleanliness, close and uniform clearance, and full penetration of the joint.

Thermal expansion
Design for thermal expansion and contraction. Leaks are commonly caused by the disparity of thermal expansion coefficients between polymers and metals. Upon cooling, the shrinkage of polymers will exceed that of metals, and seals will lose the compression required for sealing.

Flexible hose
Don’t let flexible hose flap about: include a maximum allowable slack of about 5 percent of the total length, and use restraining cables and anchors for the hose. Consider using a spring of coiled stainless steel tubing rather than hose, as hose is more flammable.

Maintenance
All equipment in any oxygen system that may be removed for inspection, maintenance, replacement, etc., should be provided with a vent valve for blowdown and purging, and to make sure it really is depressurised before removal (we got that wrong one time, a nasty bang, but no harm done).

Blunt flow impingement surfaces
Minimize blunt flow impingement surfaces. The risk of particle impact ignitions can be reduced if potential impact surfaces are designed with shallow impact angles to reduce the kinetic energy absorbed by the impact surface upon impact.

Technical papers

Author: Rick Newlands | 40 | updated: 06/11/16

Burrs and sharp edges
Eliminate burrs and avoid sharp edges. Burrs and sharp edges on equipment provide ignition sources for particle impact, and they also provide the ingredients for kindling chain (the promotion of ignition from materials of low ignition temperatures to materials of higher ignition temperatures) combustion propagation. Removal of this material is standard shop practice and is essential to avoid oxygen-enriched ignitions.

O-rings
Installation of an O-ring over threads with an outer diameter exceeding the inside diameter of the O-ring should be avoided if possible or the O-ring gets nicked/cut.

Press Fits
Press fits generate particulate during their assembly from the relative motion of the two highly loaded surfaces. The particulate can be partially removed by cleaning the joined parts immediately after pressing them together. Assemble press-fit, push-fit, and threaded valve parts into housing bores with the housing inverted (bore opening pointing down), so that contaminants generated during assembly fall away from the component rather than into flow paths.

Cleaning components with press-fit parts is extremely difficult. These parts should never be submerged into a cleaning solution or bath, as the cleaning solution enters between the two press-fit parts, leaches out later, and becomes a contaminant.

Blind passages
Eliminate blind passages. Long, narrow passages or blind passages are difficult to clean and to inspect for cleanliness. Additionally, they can provide a location for particulate to accumulate during operation of the equipment. This contamination can make the equipment susceptible to particle impact, rapid compression, and resonant cavity ignitions.

Crevices and cavities
Avoid crevices for particulate entrapment and resonant cavities. Cavities, especially those formed at the intersection of mating parts in assemblies, create a location where contamination can accumulate and increase ignition risks, as in blind passages.

Filters
Use filters to isolate system particulate; however, they should be placed in locations where they can be removed and inspected and where no possibility of back-flow exists.

Use filters at the following locations:
- Module inlets and outlets.
- Disconnect points.
- Points required to isolate difficult-to-clean passageways.
- Upstream of valve seats.

Choked flow
Design to minimize choked flow. Consider shut-off valves, metering valves, relief valves, and regulators to reduce particle impact ignition risks.

Captured vent systems
Opinions differ about the merits of captured vent systems: some say they should be avoided, but they do prevent dust and moisture coming into the system (see ‘ball valves’ above).

A relief valve or burst disc that is not open directly to the atmosphere, but rather has a tube or pipe connected to the outlet, is said to have a captured vent.

Technical papers

Author: Rick Newlands | 41 | updated: 06/11/16

If a captured vent is necessary, use highly ignition-resistant materials such as Monel or copper, and make sure the vent outlet empties well away from personnel (use shields or barriers as appropriate) and vents outdoors. Consider a screen on the outlet to prevent insects and/or small mammals crawling into the pipework.

Flameholders
Avoid eddies or stagnation zones in the feed pipework due to sudden changes in cross-section. These can act as flame-holders which prevent any fire from being flushed safely downstream.

Seals
Soft materials for seals are often necessary. But they can cold-flow (permanently deform) with use. Also, soft seals can extrude under high temperature and pressure, generating particulate contamination.

High-temperature seals (e.g. for the combustion chamber) are often copper, however the resulting copper oxide can dislodge and generate particulates.

Vaporisation
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

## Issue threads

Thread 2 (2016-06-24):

Identify test stand communication interface

matthewhauer, 2016-06-24:
A point that tumbled out of email'ing Nate:

How are the sensors and valve actuators connected to the outside world/interface?  How are the data signals and command signals bouncing from software to hardware and back?

This ticket shall be accepted when the interface has been identified adequately to make software microcontroller requirement decisions from.

7deeptide, 2016-06-27:
AFAIK, this will be achieved by a combination of COTS microcontrollers (e.g. beaglebone or somesuch) and our own open-source marionette DAQ board [http://marionette-daq.github.io/](url). Andrew and/or Gavin owns this issue.

matthewhauer, 2016-07-06:
https://marionette-daq.github.io/ ... the non-https page 404's

Can we get Andrew and/or Gavin tagged on this issue?

matthewhauer, 2016-07-06:
Note to Matt: ask Andrew and/or Gavin about using the LTC3 as a LFETS controller during testing.

This will additionally answer the question of interfacing with the hardware, because the LTC3 will use psas_packet to exchange data from the flight* hardware to the user interfaces.

LateralGs, 2016-07-06:
Have we identified what the control loops in the system are and if they are safety critical or real time in nature?

matthewhauer, 2016-07-06:
@LateralGs

>Have we identified what the control loops in the system are and if they are safety critical or real time in nature?

I bounced this off Erin last night, who said "Yes and yes".  I opened #6 since PSAS/LFETS/LTC probably need a longer answer, and we should have the answer to that question somewhere publicly visible.

matthewhauer, 2016-07-06:
I talked about this issue with Andrew last night.

The instrumentation on the test stand will be plugged into a Marionette DAQ board.  See https://marionette-daq.github.io/ for more information.

The DAQ board will either be plugged into the LTC via USB, or into a testing laptop via USB.  "A UNIX based system" [Andrew], the details are flexible.  If plugged into a laptop directly, the interface shall look for the two serial ports that Marionette exposes, pull data from one, and push commands to the other.  If plugged into LTC, the LTC is expected to broadcast telemetry data, that a software dashboard can pick up.  Or other telemetry monitors.  This telemetry data is expected to be some form of psas_packet.

In return, commands are expected to use a psas_packet command type.

Both packet types are currently unspecified.  The LFETS telemetry is likely to be a new packet type, since the existing descriptions do not specify pressure information.  The command packet type may be a new type, or may be a modification to an existing command format.  Either way, this is a topic to bring up with @jameysharp !

So.  Hardware -Cu- Marionette -USB- {?LTC -wifi-} Dashboard from layout.  The test stand shall communicate either with the Marionette DAQ directly, or with psas_packet telemetry messages.

The contents of both the telemetry and the command messages are yet unspecified.  (which means MOAR TIKKETZ)

matthewhauer, 2016-07-06:
Ticket accepted with https://github.com/psas/liquid-engine-test-stand/issues/2#issuecomment-230835335

Microcontroller requirements: Marionette DAQ, with python library to access exposed 'serial port' connections to the board.
Additionally, the data from Marionette shall be packaged up in a psas_packet telemetry message.

Followup tickets: #9 and #10

Closed 2016-07-06.

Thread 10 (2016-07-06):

(2) Build Phase: Specify LFETS/LTC telemetry packets

matthewhauer, 2016-07-06:
The LFETS will have both a 'direct' (plug in to Marionette DAQ via USB) and 'telemetered' configuration. In the latter, a psas_packet type shall be used to send telemetry data to any connected listeners and dashboards.

The contents of these telemetry messages needs to be specified. In doing so, the test stand sensors, transducers, and other sensing devices will be documented.  Note that this is concerning the output from the DAQ and the LTC, not the output from the wires themselves.  Sorry EE's, that's still on your plate.

The psas_packet is expected to map to the Marionette DAQ output serial messages.  If the two differ, the details shall be documented (which will be addressed in another ticket).

This ticket shall be accepted when a psas_packet 'LFETS telemetry' type has been written up. A follow-up ticket shall be to implement said type

matthewhauer, 2016-07-06:
Tagging @jameysharp as psas_packet SME.

matthewhauer, 2016-07-13:
Lean on @KyleMeeuwsen about the input signal list  required for the telemetry packets.

Closed 2020-09-16.

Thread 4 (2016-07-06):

Central Engine Notebook

matthewhauer, 2016-07-06:
Erin wants to see a Jupityr notebook whitepaper with
- links to relevant repos
- current to-do items
- state of the project
- work breakdown structure
- conceptual design narrative
- relevant calculations
- relevant scripts (or links to)

This notebook has been started over with the pressure calculation notebook (also here in LETS)

matthewhauer, 2016-07-06:
Notebook is "feed system calculations"

Closed 2020-09-16.

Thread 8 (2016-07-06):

Encourage small frequent commits

matthewhauer, 2016-07-06:
Identify ways to encourage LFETS members to commit and push changes to the repository more often than at the end of the term.

"Small, frequent, well-described commits are MUCH easier to perform than monolithic commits.  They also have the added benefit of sharing your changes with the team, with having an off-site backup, and having change tracking."  -Matt

This ticket shall be accepted when an effective method of encouraging git commits/pushes is identified.

matthewhauer, 2016-07-06:
I'm not sure if it'd encourage commits, but declaring that project files should be exchanged by pushing to and pulling from GitHub, and discouraging emailing project files between members, may nudge everyone in 'the right direction'.

Or students will be students and do what's easy, which would be to continue to email files.  TBD.

IanOsgood, 2016-07-06:
> declaring that project files should be exchanged by pushing to and pulling from GitHub, and discouraging emailing project files between members

That is absolutely the right thing to do. Teach these students good habits now please; their future employers and future generations of PSAS students will thank you for it!

Also, if they are worried about committing things before they have been tested, they should be taught how to use branches in git for experimental work.  Or even how to make personal forks of the PSAS repositories from which pull requests can be made.  Perhaps you should have a git seminar once a quarter to educate new students about these kind of development techniques.

matthewhauer, 2016-07-06:
> That is absolutely the right thing to do. Teach these students good habits now please; their future employers and future generations of PSAS students will thank you for it!

>Also, if they are worried about committing things before they have been tested, they should be taught how to use branches in git for experimental work. Or even how to make personal forks of the PSAS repositories from which pull requests can be made. Perhaps you should have a git seminar once a quarter to educate new students about these kind of development techniques.

There is a LOT of non-software material that gets posted to the PSAS github repos -- Jupityr (sp) notebooks, some with code and others without, technical schematics, SolidWorks files, launch data and analysis, etc. etc.  Git/VCS is a rough fit with hardware, but still works well enough.  The challenge is in getting the students just to use the system first, rather than all the other informal solutions.

The "bazillions of projects" approach that PSAS employs also presents some organizational challenges, at least when it comes to figuring out what's going on, what's "live" vs stale, and what needs attention.

I'd be game for drafting a "git and tickets" presentation for PSAS if it was useful, though I can't say that I've learned the best habits myself.

Closed 2020-09-16.

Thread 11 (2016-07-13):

(1) Acquisition Phase: We do not have a pneumatically actuated Ethanol Valve

KyleMeeuwsen, 2016-07-13:
This valve needs to be pneumatically actuated with at least an 3/8" inlet and outlet diameter.

Swagelok potentially has the ability to provide this valve with a pneumatic actuator as a package. **This actuator needs to have an open/close time of less than 4 seconds (preferably around 2 seconds).

matthewhauer, 2016-07-13:
Has a particular part number/piece, or a set of viable pieces, been identified?  Is this a part selection or procurement issue?

Closed 2016-08-31.

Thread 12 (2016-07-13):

(2) Build Phase: CAD Layout

matthewhauer, 2016-07-13:
Tyler, Kyle.

Construct a CAD drawing with simplified models of the parts to lay out the structure of the test stand and how they fit together.  Make sure the human-accessible parts are all together.

Simple primitive solids are suitable for this task at this point.

This ticket shall be accepted when a  3D diagram has been posted to the GitHub account.

KyleMeeuwsen, 2016-07-27:
Asa, I have been unsuccessful at moving the adobe file to github. For some reason Github will not take the adobe file. I have not tried the solidworks file and will attempt this either tonight or possibly tomorrow.

asa-grant, 2016-07-27:
Thanks man. Thanks for doing this for me, I need to sit down with github for an hour or so and just familiarize myself with it that way I can do it on my own.

-Asa

On Jul 26, 2016, at 11:01 PM, Kyle Meeuwsen <notifications@github.com<mailto:notifications@github.com>> wrote:

Asa, I have been unsuccessful at moving the adobe file to github. For some reason Github will not take the adobe file. I have not tried the solidworks file and will attempt this either tonight or possibly tomorrow.

—
You are receiving this because you are subscribed to this thread.
Reply to this email directly, view it on GitHub<https://urldefense.proofpoint.com/v2/url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>, or mute the thread<https://urldefense.proofpoint.com/v2/url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>.

7deeptide, 2016-07-27:
Guys, please let me know if you'd ever like a sit-down git tutorial from me... I'd be happy to do it at the next propulsion meeting if you like (you'll just need to bring your laptops).

asa-grant, 2016-07-27:
That would awesome!

Thanks!

-Asa

On Jul 27, 2016, at 3:02 PM, Erin <notifications@github.com<mailto:notifications@github.com>> wrote:

Guys, please let me know if you'd ever like a sit-down git tutorial from me... I'd be happy to do it at the next propulsion meeting if you like (you'll just need to bring your laptops).

—
You are receiving this because you commented.
Reply to this email directly, view it on GitHub<https://urldefense.proofpoint.com/v2/url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>, or mute the thread<https://urldefense.proofpoint.com/v2/url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>.

Closed 2017-02-02.

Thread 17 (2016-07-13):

(1) Acquisition Phase: Determine appropriate valve actuation times

matthewhauer, 2016-07-13:
Ask Bob and ARocket about reasonable times for ball valve actuator for the ethanol and LOX main valves.  We don't want to screw up the combustion chamber with questionably timed LOX and ethanol flow.

This ticket shall be accepted when ...

KyleMeeuwsen, 2016-08-24:
The two second open time on the LOX actuator is acceptable since based on Gregory and Robert's feedback as long as the valve is a ball valve. The ball valve allows us to crack the valve open, allowing a small amount of LOX to flow through the system, eliminating the two phase flow.

KyleMeeuwsen, 2016-08-31:
Selected 3/8" brass ball valve with 6.4 Cv. Asa needs to send the part number and MFG to Kyle.

Closed 2016-12-23.

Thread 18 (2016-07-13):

(1) Acquisition Phase: Need burst discs for LOX and Ethanol manifold

KyleMeeuwsen, 2016-07-13:
**Acceptance Criteria:**
4 burst discs from Oseco that are rated to release at 1000 PSI.
Detailed information about housing and connection fittings.
Releasing to atmosphere --> Must have a protective casing around disc to ensure there are no projectiles.

KyleMeeuwsen, 2016-07-27:
Hello Trevor,

Have you been able to make any progress on this since we last spoke. Were you waiting on some input from me?

KyleMeeuwsen, 2016-08-03:
I checked with Oseco and the quote is substantially larger than the $25 we'd heard prior. For a set of 4 good discs, with scoring to prevent rupture fragmentation, we'd be looking at $227 each ($908 for four with holders). I've put in for quotes with five other companies. Two came back in the same range of prices, a little higher. The other three claim to have quotes Wednesday (Aug 3) for me.
It's looking like the cost of discs and holders will be significant.
I'll keep looking to see if anything could be reasonably below that cost, otherwise that's the only option.

Best,
Trevor

KyleMeeuwsen, 2016-08-03:
Trevor,

Erin and I spoke and we were wondering if you wanted to get in touch with Robert Watzlavick. We are wondering if Robert specified a higher burst pressure (allowing for a thicker burst wall, requiring less machining accuracy) or if maybe Oseco is specing this for cryogenic application. I think that is great that you are looking into other companies. You are making great progress. Perhaps Erin Schmidt can provide you with Robert's email.

Best,
Kyle

TrevorLeake, 2016-08-03:
I didn't speak with Robert Watzlavick, but I will get his email from Erin. Oseco was spec'ing for 0F, though you are right that cost goes up a ton with cryogenic applications. I'll keep talking with other companies to look for a lower cost, and see if Robert can shed any light on the price difference.

I think it must be precision machining that drives the cost here, cause the material on most discs, and the ones quoted, are 316SS, and this is the bare bones simple version of a rupture disc.

All the best,
Trevor

KyleMeeuwsen, 2016-08-22:
Hello Trevor,

Any new information on this?

Best,
Kyle

Sent from my iPhone

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

TrevorLeake, 2016-08-22:
Sorry, I've been trouble making any useful findings. Basically Erin's guess was correct; a lot of manufacturers have gear which makes precision machining at the level we need more costly. I've been inquiring with a few of the companies' reps about a cheaper geometry. I am hoping that if I can't find a cheap place for purchase, we can just use a line adapter to a different (I think smaller) diameter... whichever provides easier machining.

Having the reps' available I figured I could do without bothering Robert, but I will now bother Robert.

Again, sorry for the kindof ridiculous turn-around on what appeared an simple buy.

Best wishes,
Trevor

KyleMeeuwsen, 2016-08-22:
No worries, thanks for continuing to look into this. This level of difficulty for finding a part at an appropriate cost is pretty standard it seems. Thanks for continuing the search.

Kyle

Sent from my iPhone

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

TrevorLeake, 2016-08-23:
Alright, this can be done cheap. I'll post full details in a couple days when it's all ensured.

KyleMeeuwsen, 2016-08-24:
Awesome, that's really exciting! Thank you for diving in to this.

Best,
Kyle

On Tue, Aug 23, 2016 at 1:41 PM, Trevor Leake <notifications@github.com>
wrote:

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

KyleMeeuwsen, 2016-09-21:
We have replaced the burst discs with a cryo rated pressure relief valve on the LOX side and a normal pressure relief valve on the Ethanol side.

Closed 2016-09-21.

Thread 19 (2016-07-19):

(1) Acquisition Phase: Have not reviewed the BOM level PID with the group.

KyleMeeuwsen, 2016-07-19:
Acceptance criteria:

At a minimum, Asa and Erin review the PID and support all selected fittings and assembly structure.

KyleMeeuwsen, 2016-07-20:
Move the single pressure regulator to both sides of the N2 union to allow for individual regulation on the Ethanol and LOX.

Closed 2016-12-23.

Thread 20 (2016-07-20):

(1) Acquisition Phase: Determine whether the pressure regulators need to go before or after the solenoids

KyleMeeuwsen, 2016-07-20:
Acceptance criteria:
Cv used to calculate pressure drop across solenoid valve on N2 lines to determine if we currently have workable, or if there even exists acceptable solenoid valves.

Closed 2016-12-23.

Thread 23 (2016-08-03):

(1) Acquisition Phase: Outsource hydro testing on LOx and Aluminum.

KyleMeeuwsen, 2016-08-03:
Ensure that company understands that we have modified the aluminum tank (drilling through bottom).

taruhhdactyl, 2017-06-15:
The tanks will need to run at about 700 psi, but we need a safety factor. We can probably just have them tested against the DOT standard printed on the tanks.

Below is a list of companies that will do hydro testing for $20 (so we hear) and are aware of the special procedures for galvanized tanks as well as checking the REE # to give a tank a + rating on the hydro.

US Cylinder in Vancouver
Sanderson Fire and Safety downtown Portland - **503-889-3110**
United Fire and Safety on MLK - **503.249.0771** - Tara emailed 6/15

MechBertrand, 2017-06-15:
From [Hydrostatic Testing FAQ](http://www.tymsinc.com/hydrostatic-faq.html)

> All cylinders have ratings that start with “DOT” or “ICC,” followed by the service pressure of the container.  For example “DOT 3AA 1800” means a DOT approved cylinder made to the “3AA” specification rated for 1800 psi.

7deeptide, 2017-06-15:
We have the equipment to do hydro testing ourselves. At this point no need
to outsource it...

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
--
Ad astra
Erin Schmidt

Closed 2020-09-16.

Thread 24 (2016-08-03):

(1) Acquisition Phase: FEA Analysis and Sizing of Load Cells

DylanStephens, 2016-08-03:
There will be four load cells measuring the engine's thrust. The design's measurements are in English units. The force should be applied to the bottom face of the hole that is above the relief cut. The file that needs to be analyzed can be found here: https://github.com/psas/liquid-engine-test-stand/tree/master/SW%20CAD/Test%20Stand%20Assembly Labeled as Loadcell7. The load cell needs to be analyzed for the maximum stress without yielding.

KyleMeeuwsen, 2016-08-03:
After solving, send results to Dylan and discuss iterative analysis approach.

KyleMeeuwsen, 2016-08-03:
Later- Temperature concerns to be addressed later.
May necessitate a protective casing for environment isolation and thermocouples and possibly LOX lines for cooling around casing?

Closed 2020-09-16.

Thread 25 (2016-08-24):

(1) Acquisition Phase: Finish P&ID

KyleMeeuwsen, 2016-08-24:
Incorporate the ignitor system into the P&ID. (Kyle B) will be providing a schematic of the ignitor system and I will add it to the P&ID.

We will not be adding a wiring diagram since this will be developed by another group.

7deeptide, 2017-04-01:
@JacobTiller @asa-grant
Issues with the system level PID:
1. Mix of ISO and ASME symbols (MFV & MOV use ASME for instance)
2.Purge system check valves are backwards
3. There will be either an orifice or flow meter on the fuel side just prior to the engine fuel manifold inlet
4. No fuel line to engine

Bigger issue with the system itself: We can not stage the engine startup with this layout. We have to open the main valves before we can start the igniter. Obviously this is problematic if we want to verify good ignition before opening the main valves. Maybe we should move the igniter lines behind the main valves and give them their own purge lines?

JacobTiller, 2017-04-04:
@7deeptide @asa-grant

1. I believe I have the MFV and MOV valve symbols correct (based on what I know about them at least)
2. Fixed purge valve orientation
3. added a place holder for an orifice or flow meter on the fuel side
4. added the missing fuel line.

As for the bigger issue,  I took a stab at changing the igniter lines and adding a second purge line to the system.   I created an "Alt A" system PID and pushed it.

7deeptide, 2017-04-04:
@JacobTiller @asa-grant The Alt-A schematic is a good start. We don't need to separately purge the igniter and main tubes, they can all be controlled by a single valve (e.g. valve 9).@

Also needing to be added:
1. Heat exchanger coil on the LOX igniter tube.
2. Pressure transducer and K-thermocouple on the pre-injection fuel manifold.

JacobTiller, 2017-06-15:
Closing issue as all of the items on it were completed.  PID has a number of other items still needed so I'm opening a new issue for the new updates needed.

Closed 2017-06-15.

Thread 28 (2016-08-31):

(1) Acquisition Phase: Spec and select a Lox Fill Vent Valve

KyleMeeuwsen, 2016-08-31:
From Robert's Page:
Here is the current plumbing layout. The pressurization lines will use 1/4 inch and the liquid lines will use 3/8 inch 6061-T6 aluminum tubing. Igniter lines will be 1/8 inch 3003-O tubing. The LOX vent will be located between the fuel and LOX tanks to keep the cold liquid away from the regulator, pressure transducer, and burst disc.

KyleMeeuwsen, 2016-08-31:
ARocket - Robert and Others:

It seems sticking LOX valves are a recurring problem - CS had issues recently and I've experienced the problem several times myself.  On my recent set of cold tests, I noticed that the first run of the day with LN2 was OK but if I didn't let the exterior of the valve dry out sufficiently between runs, moisture condensed from the atmosphere would find its way into the valve bearing and cause it to freeze up.  It would be a major redesign to add another seal to keep moisture out of the stem/bearing section of the valve body (there's not much room).  I was thinking an inexpensive modification would be to enclose the LOX vent, fill, and main valves in plastic wrap of some sort with small plastic tubes coming out of them.  Then, I could squirt some N2 into them from a central point prior to the test to displace the moisture-laden air.  Since it wouldn't be a completely sealed system, some air would leak back in but it seems like it would be an improvement over nothing.  Clear PTFE bags are available but I'd need some way to seal the openings.  Wide (1 inch or greater) PTFE tape might work also, just wrapping it around a bunch of times.  Kitchen wrap would also work but I'm not sure about whether it would crack when cold or whether it is oxygen compatible.

over the seams? Or stainless foil, like the sort of stuff used for
keeping out oxygen when heat treating small parts? Or you could do the
whole covering out of foil; I'm not sure which option would be easier
in practice.

Aluminum foil seems like a better idea - thanks.  It doesn't need to be completely airtight - in fact, it probably needs a little drain hole at the bottom in case there is LOX leak so it doesn't fill up.  And foil vs. PTFE wrap would allow the servo to survive slightly longer (although not much) in case of a fire.

Also be aware of "cryopumping"--cold surfaces cool the air around them, causing a drop in pressure and sucking in more air. I'm not sure if you were planning on just a "static" volume of GN2 around your valve (not an active purge). If so, it's possible moist air could still be sucked into the enclosure. How much and whether it would be a problem, I don't know.

KyleMeeuwsen, 2016-08-31:
3/8" brass piloted solenoid valve with *all* PTFE seals and correct-ish pressure rating will likely work, if you can survive the weight. Needs to be cleaned for oxygen service. You will need to buy or make an appropriate "spanner wrench" to pull the pilot stem assembly.

For a 4 gallon tank a 1/4" NPT valve with 3/8 tube adapters would likely even be sufficient. Piloted valves have higher pressure ratings for the same amount of Cv compared to direct acting, and you don't need the super low latency of a direct acting valve. A piloted solenoid valve is still faster than a pneumatic ball valve or electric plug valve.

Make sure it stays dry inside. Don't insulate the valve, you don't want the coil to get too cold because the casing is typically plastic.

KyleMeeuwsen, 2016-08-31:
# Requirements:
Not sure if we need a high Cv since this will be releasing evaporated Oxygen at a low pressure differential during LOx filling.
Need a valve rated for ~1000 PSI for operating pressure.
Required - All PTFE seals.
3/8" NPT or Ferrule fittings on both ends
Piloted Solenoid valve

KyleMeeuwsen, 2016-09-06:
For cryogenic rated valves at 1/2", estimated cost is around $800, and max differential pressure typically maximum at ambient temp and around 100 PSIG...

asa-grant, 2016-09-06:
Agreed, with the exception of valves with prohibitively small orifice sizes, I cannot find a normally open cryo-rated valve that can handle pressures anywhere near our working pressure

-Asa

On Sep 5, 2016, at 5:08 PM, Kyle Meeuwsen <notifications@github.com<mailto:notifications@github.com>> wrote:

For cryogenic rated valves at 1/2", estimated cost is around $800, and max differential pressure typically maximum at ambient temp and around 100 PSIG...

—
You are receiving this because you are subscribed to this thread.
Reply to this email directly, view it on GitHub<https://urldefense.proofpoint.com/v2/url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>, or mute the thread<https://urldefense.proofpoint.com/v2/url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>.

KyleMeeuwsen, 2016-09-07:
Swagelok does not offer straight thread and NPT is not acceptable since NPT will require PTFE which cannot be used for LOX and makes disassembly difficult. Thus we are selecting SS-45S8 with a 12Cv and Ferrule fittings.

Closed 2016-09-07.

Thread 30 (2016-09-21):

(1) Acquisition Phase: Select pilot valves for pneumatic actuator

KyleMeeuwsen, 2016-09-21:
Part Number: AVS-5211-24D

NITRA pneumatic solenoid valve, 5-port, 2-position, spring return spool, aluminum body, 1/8 inch FNPT ports, Cv=0.78, 24VDC single solenoid, DIN connector.

Andrew Greenberg familiar with DIN Connectors

KyleMeeuwsen, 2016-09-21:
Connector Part Number: 5779K102
Manufacturer: McMaster-Carr

1/8 inch male NPT --> Push to connect fittings to allow connection between pilot valve and pressure source.

Straight Adapter for 1/8" Tube OD x 1/8 NPT Male

http://www.mcmaster.com/#5779k102/=149ad2l

Closed 2016-09-21.

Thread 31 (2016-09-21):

Add GOX and Ethanol igniter solenoids

7deeptide, 2016-09-21:
The Gems A2012-2M-OC-V-VO-C204 (500 psi, 3/64 inch opening, Cv=0.035) vale was suggested by Robert Watzlavick. Thesse should work for both the GOX and IPA taps. [link](http://www.gemssensors.com/Solenoid-Valves/General-Purpose/A-Series-Solenoid-Valve)

KyleMeeuwsen, 2016-10-05:
Line size from the union cross on the LOX side to the ignitor is 1/8" with an AN flare.  The ignitor will receive both Ethanol and LOX.

Need to get flow rates from Kyle Blakemen.

asa-grant, 2016-10-05:
We wouldn't do a 1/8" union cross. We need 1/2" union crosses and then 1/2" to 1/8" tube adapters FYI.

On Oct 4, 2016, at 6:16 PM, Kyle Meeuwsen <notifications@github.com<mailto:notifications@github.com>> wrote:

Line size from the union cross on the LOX side to the ignitor is 1/8" with an AN flare. The ignitor will receive both Ethanol and LOX.

Need to get flow rates from Kyle Blakemen.

—
You are receiving this because you are subscribed to this thread.
Reply to this email directly, view it on GitHub<https://urldefense.proofpoint.com/v2/url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>, or mute the thread<https://urldefense.proofpoint.com/v2/url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>.

Closed 2020-09-16.

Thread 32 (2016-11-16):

Cut Load Cell Supports to drawing specified dimensions

DylanStephens, 2016-11-16:
The load cell supports need to be cut. Drawings for the two parts are located in the liquid-engine-test-stand\Parts to be machined\Load cell support short and Load cell support long. C-channel materials are in the Rocket room. Contact Dylan Stephens at dylanjsteph@gmail.com.

To be Accepted when parts are cut to the drawing specifications and verified by Dylan Stephens.

Closed 2020-09-16.

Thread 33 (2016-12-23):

CAD Assembly has missing dependencies

7deeptide, 2016-12-23:
Many missing dependencies... @asa-grant Do you have these on your local machine?

Instances of the following were suppressed when the assembly was opened:

C:\Users\Dylan\Desktop\LMTS CAD\Actual Rigid wheel.SLDPRT
C:\Users\asa\Desktop\Flowserve\Ball valve Assembly.SLDASM
C:\Users\asa\Desktop\LETS SW Parts\G17M0215F23000_PRT_28.SLDPRT
C:\Users\asa\Desktop\LETS SW Parts\Panel Assembly\Inner Panel Assembly.SLDASM
C:\Users\asa\Desktop\LETS SW Parts\SS4001421159_PRT_20.SLDPRT
C:\Users\asa\Desktop\LETS SW Parts\SS400921753_PRT_Needed.SLDPRT
C:\Users\asa\Desktop\LETS SW Parts\SS4C41_PRT_31.SLDPRT
C:\Users\asa\Desktop\LETS SW Parts\SS4TA7420118.SLDPRT
C:\Users\asa\Desktop\LETS SW Parts\SS_8_TA_7_4_2157321573.SLDPRT
C:\Users\asa\Downloads\4024T730_FIRE-TESTED STEEL BALL VALVE.SLDPRT
C:\Users\asa\Downloads\46105K650_HIGH-PRESSURE COMPACT CHECK VALVE.SLDPRT
C:\Users\asa\Downloads\4936K154_BSPT-BSPP-METRIC HI-PRESSURE STL THRD FITTING.SLDPRT	C:\Users\asa\Downloads\50785K275_MED-PRESSURE BRASS THREADED PIPE FITTING.SLDPRT
C:\Users\asa\Downloads\90591A141_ZINC PLATED STEEL HEX NUT.SLDPRT
C:\Users\asa\Downloads\90854A132_HIGH-STRG ZINC YELLOW-CHROMATE PLTD CAP SCREW.SLDPRT
C:\Users\asa\Downloads\91292A116_TYPE 18-8 SS SOCKET HEAD CAP SCREW.SLDPRT
C:\Users\asa\Downloads\91783A825_18-8 SS ROUND HEAD SLOTTED MACHINE SCREW.SLDPRT
C:\Users\asa\Downloads\92005A248_METRIC PAN HEAD PHILLIPS MACHINE SCREW.SLDPRT
C:\Users\asa\Downloads\tower-pro-mg-995-analog-servo-1.snapshot.6 (1)\TOWER PRO MG-995, ANALOG SERVO, BODY, BOTTOM.SLDPRT
C:\Users\asa\Downloads\tower-pro-mg-995-analog-servo-1.snapshot.6 (1)\TOWER PRO MG-995, ANALOG SERVO, BODY, MIDDLE.SLDPRTC:\Users\asa\Downloads\tower-pro-mg-995-analog-servo-1.snapshot.6 (1)\TOWER PRO MG-995, ANALOG SERVO, BODY, TOP.SLDPRT
C:\Users\asa\Downloads\tower-pro-mg-995-analog-servo-1.snapshot.6 (1)\TOWER PRO MG-995, ANALOG SERVO, CONNECTOR.SLDPRT
C:\Users\asa\Downloads\tower-pro-mg-995-analog-servo-1.snapshot.6 (1)\TOWER PRO MG-995, ANALOG SERVO, HORN.sldprt
C:\Users\asa\Downloads\tower-pro-mg-995-analog-servo-1.snapshot.6 (1)\TOWER PRO MG-995, ANALOG SERVO, SHAFT.SLDPRT

Closed 2017-02-02.

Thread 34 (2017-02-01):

Machine LOX and Fuel tank Brackets

DylanStephens, 2017-02-01:
There are SolidWorks Part files for the LOX top plate, LOX mid plate, and Fuel top plate are located here https://github.com/psas/liquid-engine-test-stand/tree/master/Parts%20to%20be%20machined . These parts need to be brought into Mastercam and tool paths need to be drawn. The parts then need to be milled on the CNC Mill using the materials that are labeled in the Rocket room. If you have any questions email Dylan at dylanjsteph@gmail.com . This ticket is to be accepted when all three of the LOX and Fuel Plates have been machined to the proper specifications and verified by Dylan Stephens.

Closed 2020-09-16.

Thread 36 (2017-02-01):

Design the Liquid engine to Thrust Ring adapter

DylanStephens, 2017-02-01:
An adapter needs to be designed (make sure it can easily be manufactured) to connect the Engine thrust ring (Found here: https://github.com/psas/liquid-engine-test-stand/tree/master/Parts%20to%20be%20machined ) to the Liquid engine (Found here: https://github.com/psas/liquid-engine-capstone-2015/blob/master/SolidWorks_Files/Engine_Print_1/2016-06-08/Nozzle_Manifold.SLDPRT ). This part will need to attach to the inside of the thrust ring via the holes in the solidworks file and to the holes on the top of the liquid engine that can be seen in the attached image. There will need to be a space designed into the adapter to accommodate the pintle which is still being designed.
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

This ticket is to be accepted when the adapter has been designed and is approved by Dylan Stephens and Erin Schmidt.

Closed 2020-09-16.

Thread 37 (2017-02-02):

Prop-tank in-line pressurant diffusers

7deeptide, 2017-02-02:
Pressurant diffusers are needed on both the LOX and IPA tanks to minimize the amount N2 mixing and diffusion that occurs in the tank (this especially important with LOX).

Diffusers need to be designed and fabricated.

For reference/inspiration:
[https://www.nasa.gov/sls/sls-diffuser.html]()
[https://ntrs.nasa.gov/archive/nasa/casi.ntrs.nasa.gov/19660000341.pdf]()

@Joedang You interested in looking at this problem?

IanZabel, 2017-05-05:
I'm ready to get going on it, but I want to ensure I have the right dimensions/parameters. From the parameters in [the math section](https://github.com/psas/liquid-engine-test-stand/blob/master/analysis/feed_system_calculations.ipynb), you've got the mass flow rates for both the LOX and IPA tanks as well as tube diameters [(where gas flow is labeled?)](https://ntrs.nasa.gov/archive/nasa/casi.ntrs.nasa.gov/19660000341.pdf).

- What were the threads required, using the NASA example linked as a reference (just past the flange)?
- Am I referencing the correct mass flow rates and pressures?
- Any specific requirements for the flange/plug?

With that I can start on the CAD and whip something up.

CStarker, 2020-03-29:
Is this still necessary or should this be marked as complete?

Closed 2020-09-16.

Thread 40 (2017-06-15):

Complete Piping and Instrumentation Diagram

JacobTiller, 2017-06-15:
**Issue:** System PID is in need of updates to reflect changes.

**Description:** The system level PID needs to reflect the currently selected parts laid out in the Bill of Materials.
  - PID reference numbers need to be correctly assigned for each item on the PID
  - Each PID reference number needs to have a corresponding line in the Bill of Materials, even if the item is not yet specified.
  - New PID legend (PDF) file needs to be created and posted on GIT

**Deliverable**
1. SVG & PDF file containing System PID with all components correctly labeled.
2. PDF copy of updated PID legend with all System PID components listed.

Closed 2020-09-16.

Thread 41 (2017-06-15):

Main Fuel Valve

JacobTiller, 2017-06-15:
**Project** : Design and build electrically actuated main fuel valve

**Description** : The final valve connecting the pressurized fuel line to the test engine needs to be activated and controlled remotely.  This project is to design and build a servo / motor driven valve which is capable of opening the main fuel valve.

**Requirements** :

The valve which has been selected for use as the main fuel valve is a Sharpe 39036 1/2 in ball valve.  (see doc file for specification sheet).

** constraints:**
  - Opening torque for ball valve - 35 in.lb's per manufacturer
 - Power supply - 12V DC or less
 - For testing, the hardware should be able to be run with an Arduino

**Deliverable:** The valve needs to be able to be reliably opened and closed.  Will need to be able to withstand strenuous testing.

MechBertrand, 2017-07-10:
initial wOrk done on the DC motor. Check out the readme to see how to NOT make a valve work XD

Closed 2020-09-16.

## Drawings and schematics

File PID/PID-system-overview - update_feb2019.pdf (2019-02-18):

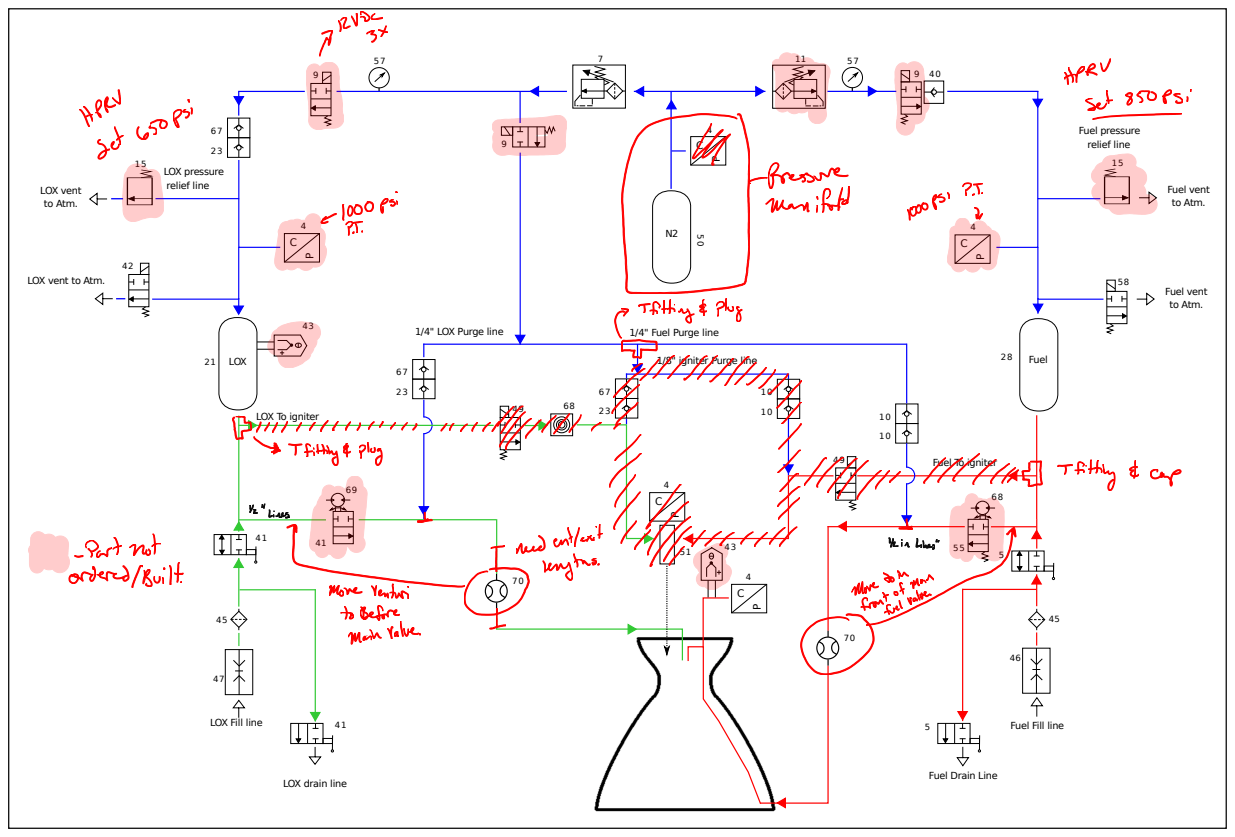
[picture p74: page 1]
LOX pressure relief line; LOX; LOX vent to Atm.; Fuel; Fuel pressure relief line; Fuel vent to Atm.

LOX vent to Atm.

1/4" LOX Purge line

1/4" Fuel Purge line

1/8" igniter Purge line

LOX To igniter

Fuel To igniter

LOX Fill line

Fuel Fill line

LOX drain line

Fuel Drain Line

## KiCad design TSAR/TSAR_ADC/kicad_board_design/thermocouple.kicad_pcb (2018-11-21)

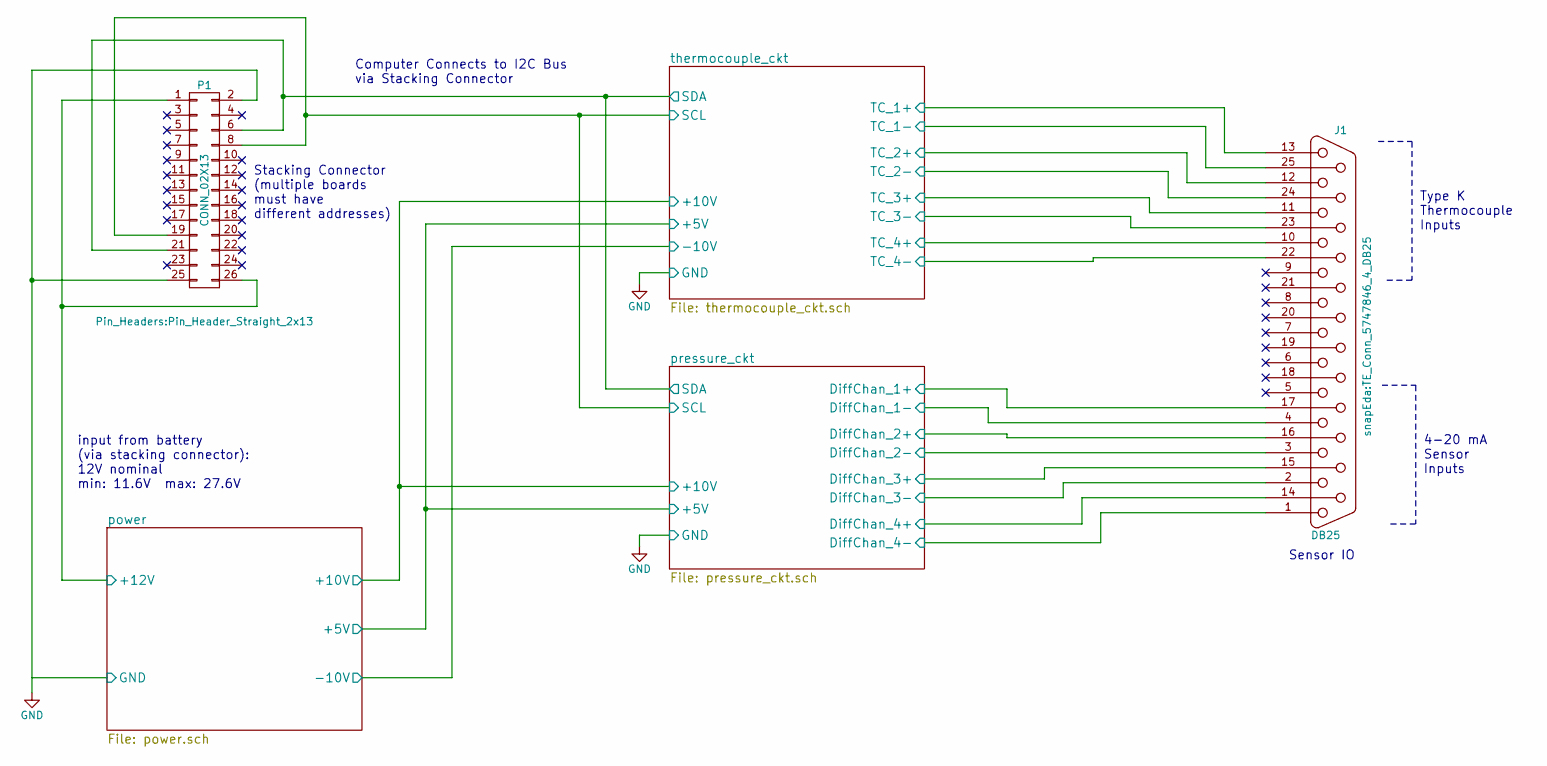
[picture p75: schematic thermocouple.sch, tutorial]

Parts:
J1: DB25; TE_Conn_5747846_4_DB25; MPN 5747846-4
P1: CONN_02X13; Pin_Header_Straight_2x13

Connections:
/power/+12V: P1.1, P1.26; also elsewhere on the board
/pressure_ckt/DiffChan_1+: J1.17; also elsewhere on the board
/pressure_ckt/DiffChan_1-: J1.4; also elsewhere on the board
/pressure_ckt/DiffChan_2+: J1.16; also elsewhere on the board
/pressure_ckt/DiffChan_2-: J1.3; also elsewhere on the board
/pressure_ckt/DiffChan_3+: J1.15; also elsewhere on the board
/pressure_ckt/DiffChan_3-: J1.2; also elsewhere on the board
/pressure_ckt/DiffChan_4+: J1.14; also elsewhere on the board
/pressure_ckt/DiffChan_4-: J1.1; also elsewhere on the board
/pressure_ckt/SCL: P1.8, P1.19; also elsewhere on the board
/pressure_ckt/SDA: P1.6, P1.21; also elsewhere on the board
/thermocouple_ckt/TC_1+: J1.13; also elsewhere on the board
/thermocouple_ckt/TC_1-: J1.25; also elsewhere on the board
/thermocouple_ckt/TC_2+: J1.12; also elsewhere on the board
/thermocouple_ckt/TC_2-: J1.24; also elsewhere on the board
/thermocouple_ckt/TC_3+: J1.11; also elsewhere on the board
/thermocouple_ckt/TC_3-: J1.23; also elsewhere on the board
/thermocouple_ckt/TC_4+: J1.10; also elsewhere on the board
/thermocouple_ckt/TC_4-: J1.22; also elsewhere on the board

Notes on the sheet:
Stacking Connector (multiple boards must have different addresses)
Sensor IO
input from battery (via stacking connector): 12V nominal min: 11.6V max: 27.6V
Type K Thermocouple Inputs
4-20 mA Sensor Inputs
Computer Connects to I2C Bus via Stacking Connector

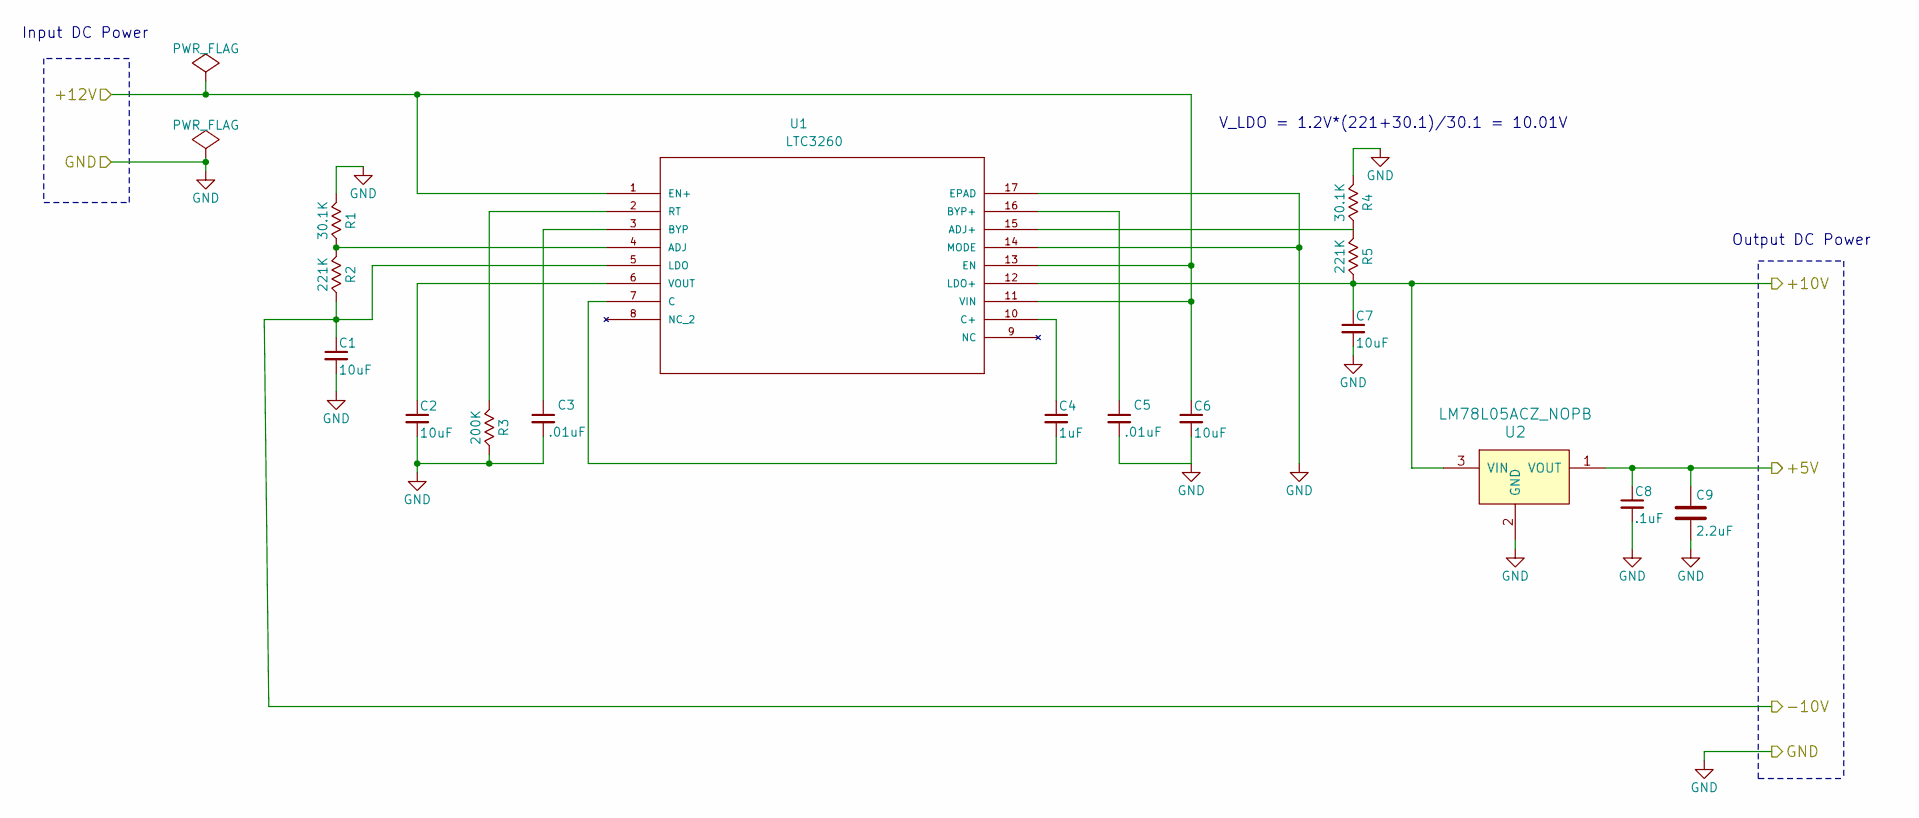
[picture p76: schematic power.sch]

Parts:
C1, C2, C6, C7: 10uF; C_0603_HandSoldering; MPN CL10B106MQ8NRNC
C3, C5: .01uF; C_0402; MPN CL05B103KB5NNNC
C4: 1uF; C_0603_HandSoldering; MPN CL10B105KP8NNNC
C8: .1uF; C_0402; MPN CL05B104KO54PNC
C9: 2.2uF; C_0805_HandSoldering; MPN C2012X7R1C225K125AB
R1, R4: 30.1K; R_0805_HandSoldering; MPN ERA-6AEB3012V
R2, R5: 221K; R_0805_HandSoldering; MPN ERA-6AEB2213V
R3: 200K; R_0805_HandSoldering; MPN KTR10EZPF2003
U1: LTC3260; MSOP-16_MSE; MPN LTC3260EMSE#PBF
U2: LM78L05ACZ_NOPB; TO-92-3; MPN LM78L05ACZ/NOPB; Digi-Key_PN LM78L05ACZNS/NOPB-ND

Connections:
/power/+5V: C8.1, C9.1, U2.1 (VOUT); also elsewhere on the board
/power/+10V: C7.1, R5.2, U1.12 (LDO+), U2.3 (VIN); also elsewhere on the board
/power/+12V: C6.1, U1.1 (EN+), U1.11 (VIN), U1.13 (EN); also elsewhere on the board
/power/-10V: C1.1, R2.2, U1.5 (LDO); also elsewhere on the board
unnamed: C2.1, U1.6 (VOUT)
unnamed: C3.1, U1.3 (BYP)
unnamed: C4.1, U1.10 (C+)
unnamed: C4.2, U1.7 (C)
unnamed: C5.1, U1.16 (BYP+)
unnamed: R1.2, R2.1, U1.4 (ADJ)
unnamed: R3.1, U1.2 (RT)
unnamed: R4.2, R5.1, U1.15 (ADJ+)

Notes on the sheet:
V_LDO = 1.2V*(221+30.1)/30.1 = 10.01V
Input DC Power
Output DC Power

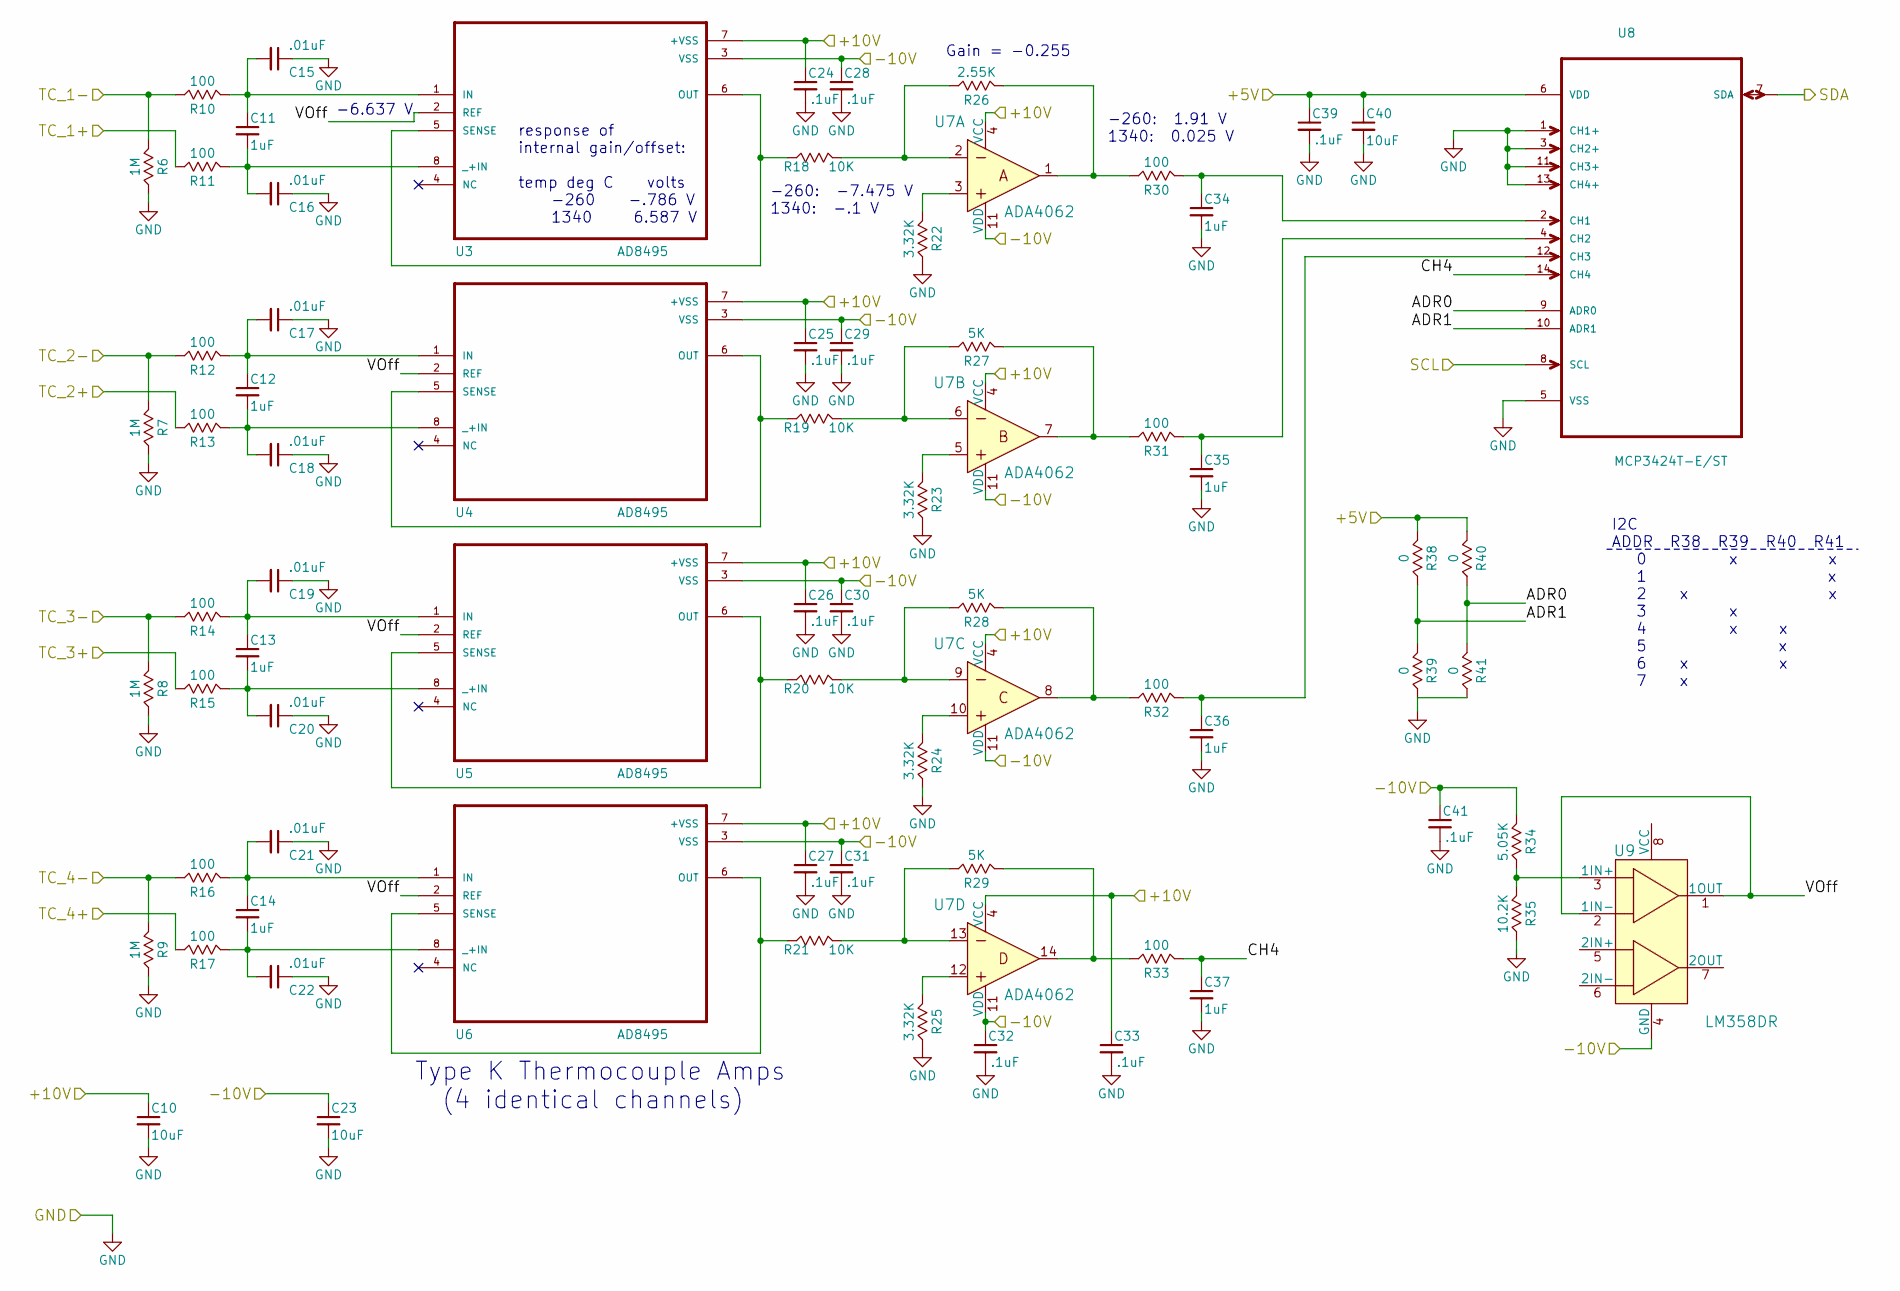
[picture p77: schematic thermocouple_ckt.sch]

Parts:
C10, C23, C40: 10uF; C_0603_HandSoldering; MPN CL10B106MQ8NRNC
C11, C12, C13, C14, C34, C35, C36, C37: 1uF; C_0603_HandSoldering; MPN CL10B105KP8NNNC
C15, C16, C17, C18, C19, C20, C21, C22: .01uF; C_0402; MPN CL05B103KB5NNNC
C24, C25, C26, C27, C28, C29, C30, C31, C32, C33, C39, C41: .1uF; C_0402; MPN CL05B104KO54PNC
R6, R7, R8, R9: 1M; R_0805_HandSoldering; MPN CRGH0805F1M0
R10, R11, R12, R13, R14, R15, R16, R17, R30, R31, R32, R33: 100; R_1206; MPN LTR18EZPF1000
R18, R19, R20, R21: 10K; R_0603_HandSoldering; MPN ERA-3ARB103V
R22, R23, R24, R25: 3.32K; R_0805_HandSoldering; MPN RR1220P-3321-D-M
R26: 2.55K; R_1206; MPN RT1206BRD075KL
R27, R28, R29: 5K; R_1206; MPN RT1206BRD075KL
R34: 5.05K; R_0603_HandSoldering; MPN RT0603DRE075K17L
R35: 10.2K; R_0805_HandSoldering; MPN RN73C2A10K2BTDF
R38, R39, R40, R41: 0; R_0805_HandSoldering; MPN ERJ-6GEY0R00V
U3: AD8495; SOP65P490X110-8N; MPN AD8495ARMZ-R7
U4, U5, U6: AD8495; SOP65P490X110-8N
U7: ADA4062; ADA4062-4ARUZ; MPN ADA4062-4ARUZ
U8: MCP3424T-E/ST; SOP65P640X120-14N
U9: LM358DR; SOIC-8_W3.9mm; MPN LM358DR; Digi-Key_PN 296-1014-1-ND

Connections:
/power/+5V: C39.1, C40.1, R38.1, R40.1, U8.6 (VDD); also elsewhere on the board
/power/+10V: C10.1, C24.1, C25.1, C26.1, C27.1, C33.1, U3.7 (+VSS), U4.7 (+VSS), U5.7 (+VSS), U6.7 (+VSS), U7.4 (VCC), U9.8 (VCC); also elsewhere on the board
/power/-10V: C23.1, C28.1, C29.1, C30.1, C31.1, C32.1, C41.1, R34.1, U3.3 (VSS), U4.3 (VSS), U5.3 (VSS), U6.3 (VSS), U7.11 (VDD), U9.4 (GND); also elsewhere on the board
/pressure_ckt/SCL: U8.8 (SCL); also elsewhere on the board
/pressure_ckt/SDA: U8.7 (SDA); also elsewhere on the board
/thermocouple_ckt/ADR0: R40.2, R41.1, U8.9 (ADR0)
/thermocouple_ckt/ADR1: R38.2, R39.1, U8.10 (ADR1)
/thermocouple_ckt/CH4: C37.1, R33.1, U8.14 (CH4)
/thermocouple_ckt/TCA_1: R18.2, U3.5 (SENSE), U3.6 (OUT)
/thermocouple_ckt/TCA_2: R19.2, U4.5 (SENSE), U4.6 (OUT)
/thermocouple_ckt/TCA_3: R20.2, U5.5 (SENSE), U5.6 (OUT)
/thermocouple_ckt/TCA_4: R21.2, U6.5 (SENSE), U6.6 (OUT)
/thermocouple_ckt/TC_1+: R11.2; also elsewhere on the board
/thermocouple_ckt/TC_1-: R6.1, R10.2; also elsewhere on the board
/thermocouple_ckt/TC_2+: R13.2; also elsewhere on the board
/thermocouple_ckt/TC_2-: R7.1, R12.2; also elsewhere on the board
/thermocouple_ckt/TC_3+: R15.2; also elsewhere on the board
/thermocouple_ckt/TC_3-: R8.1, R14.2; also elsewhere on the board
/thermocouple_ckt/TC_4+: R17.2; also elsewhere on the board
/thermocouple_ckt/TC_4-: R9.1, R16.2; also elsewhere on the board
/thermocouple_ckt/VOff: U3.2 (REF), U4.2 (REF), U5.2 (REF), U6.2 (REF), U9.1 (1OUT), U9.2 (1IN-)
unnamed: C11.1, C15.2, R10.1, U3.1 (IN)
unnamed: C11.2, C16.2, R11.1, U3.8 (_+IN)
unnamed: C12.1, C17.2, R12.1, U4.1 (IN)
unnamed: C12.2, C18.2, R13.1, U4.8 (_+IN)
unnamed: C13.1, C19.2, R14.1, U5.1 (IN)
unnamed: C13.2, C20.2, R15.1, U5.8 (_+IN)
unnamed: C14.1, C21.2, R16.1, U6.1 (IN)
unnamed: C14.2, C22.2, R17.1, U6.8 (_+IN)
unnamed: C34.1, R30.1, U8.2 (CH1)
unnamed: C35.1, R31.1, U8.4 (CH2)
unnamed: C36.1, R32.1, U8.12 (CH3)
unnamed: R18.1, R26.2, U7.2
unnamed: R19.1, R27.2, U7.6
unnamed: R20.1, R28.2, U7.9
unnamed: R21.1, R29.2, U7.13
unnamed: R22.1, U7.3
unnamed: R23.1, U7.5
unnamed: R24.1, U7.10
unnamed: R25.1, U7.12
unnamed: R26.1, R30.2, U7.1
unnamed: R27.1, R31.2, U7.7
unnamed: R28.1, R32.2, U7.8
unnamed: R29.1, R33.2, U7.14
unnamed: R34.2, R35.1, U9.3 (1IN+)
unnamed 91: U9.5 (2IN+); also elsewhere on the board

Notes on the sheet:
-6.637 V
response of internal gain/offset: temp deg C volts -260 -.786 V 1340 6.587 V
Type K Thermocouple Amps (4 identical channels)
Gain = -0.255
-260: -7.475 V 1340: -.1 V
-260: 1.91 V 1340: 0.025 V
I2C ADDR R38 R39 R40 R41 0 x x 1 x 2 x x 3 x 4 x x 5 x 6 x x 7 x

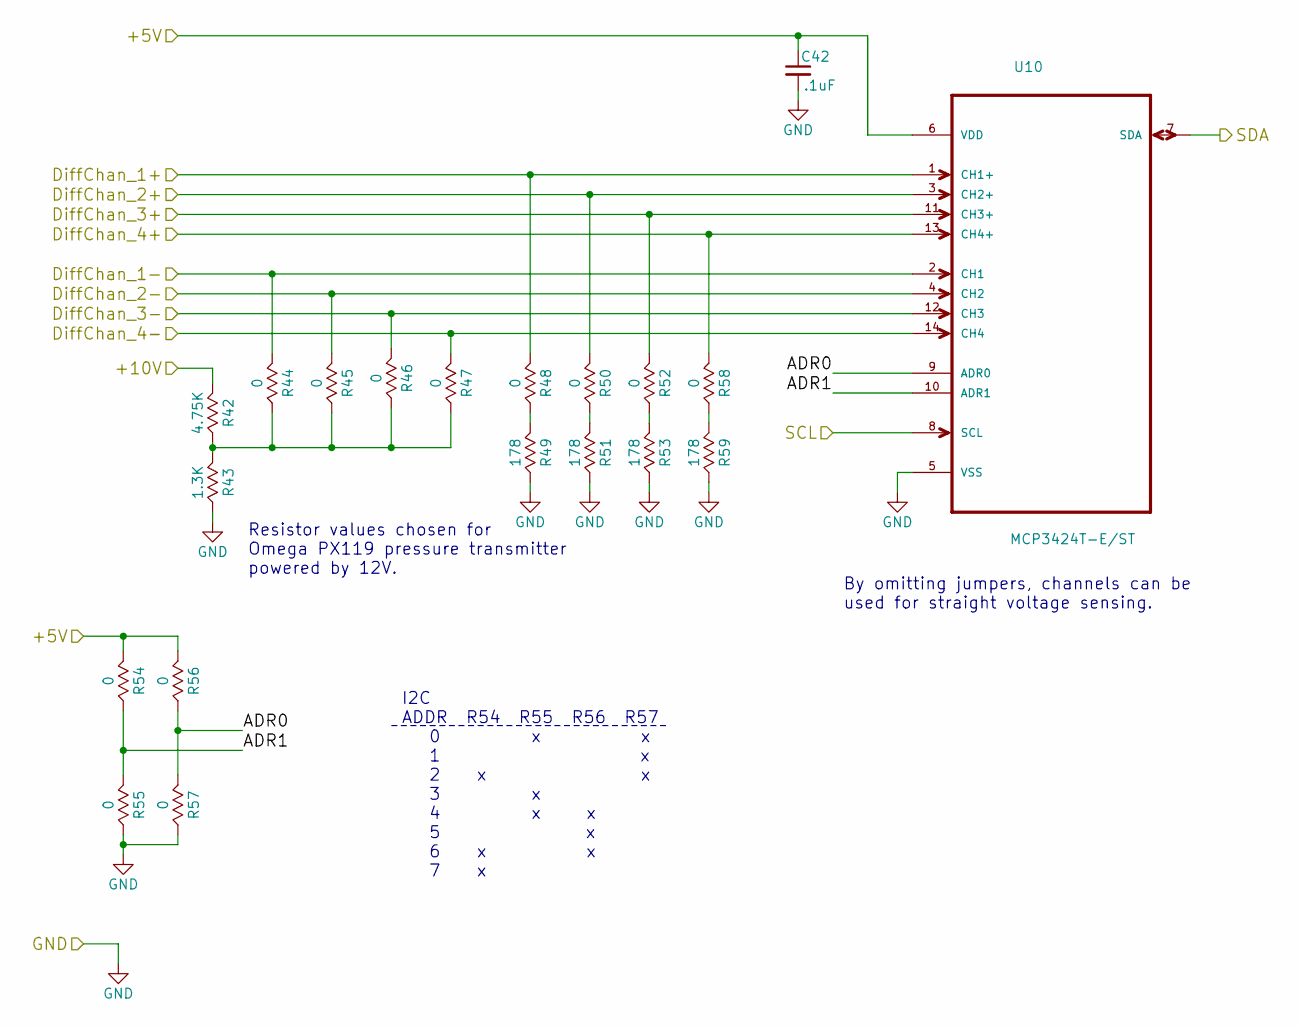
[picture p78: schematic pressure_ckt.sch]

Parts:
C42: .1uF; C_0402; MPN CL05B104KO54PNC
R42: 4.75K; R_0805_HandSoldering; MPN RG2012P-4751-B-T5
R43: 1.3K; R_0603_HandSoldering; MPN ERA-3APB132V
R44, R45, R46, R47, R48, R50, R52, R54, R55, R56, R57, R58: 0; R_0805_HandSoldering; MPN ERJ-6GEY0R00V
R49, R51, R53, R59: 178; R_0402; MPN ERA-2AEB1780X
U10: MCP3424T-E/ST; SOP65P640X120-14N

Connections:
/power/+5V: C42.1, R54.1, R56.1, U10.6 (VDD); also elsewhere on the board
/power/+10V: R42.1; also elsewhere on the board
/pressure_ckt/ADR0: R56.2, R57.1, U10.9 (ADR0)
/pressure_ckt/ADR1: R54.2, R55.1, U10.10 (ADR1)
/pressure_ckt/DiffChan_1+: R48.1, U10.1 (CH1+); also elsewhere on the board
/pressure_ckt/DiffChan_1-: R44.1, U10.2 (CH1); also elsewhere on the board
/pressure_ckt/DiffChan_2+: R50.1, U10.3 (CH2+); also elsewhere on the board
/pressure_ckt/DiffChan_2-: R45.1, U10.4 (CH2); also elsewhere on the board
/pressure_ckt/DiffChan_3+: R52.1, U10.11 (CH3+); also elsewhere on the board
/pressure_ckt/DiffChan_3-: R46.1, U10.12 (CH3); also elsewhere on the board
/pressure_ckt/DiffChan_4+: R58.1, U10.13 (CH4+); also elsewhere on the board
/pressure_ckt/DiffChan_4-: R47.1, U10.14 (CH4); also elsewhere on the board
/pressure_ckt/SCL: U10.8 (SCL); also elsewhere on the board
/pressure_ckt/SDA: U10.7 (SDA); also elsewhere on the board
unnamed: R42.2, R43.1, R44.2, R45.2, R46.2, R47.2
unnamed: R48.2, R49.1
unnamed: R50.2, R51.1
unnamed: R52.2, R53.1
unnamed: R58.2, R59.1

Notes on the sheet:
Resistor values chosen for Omega PX119 pressure transmitter powered by 12V.
By omitting jumpers, channels can be used for straight voltage sensing.
I2C ADDR R54 R55 R56 R57 0 x x 1 x 2 x x 3 x 4 x x 5 x 6 x x 7 x

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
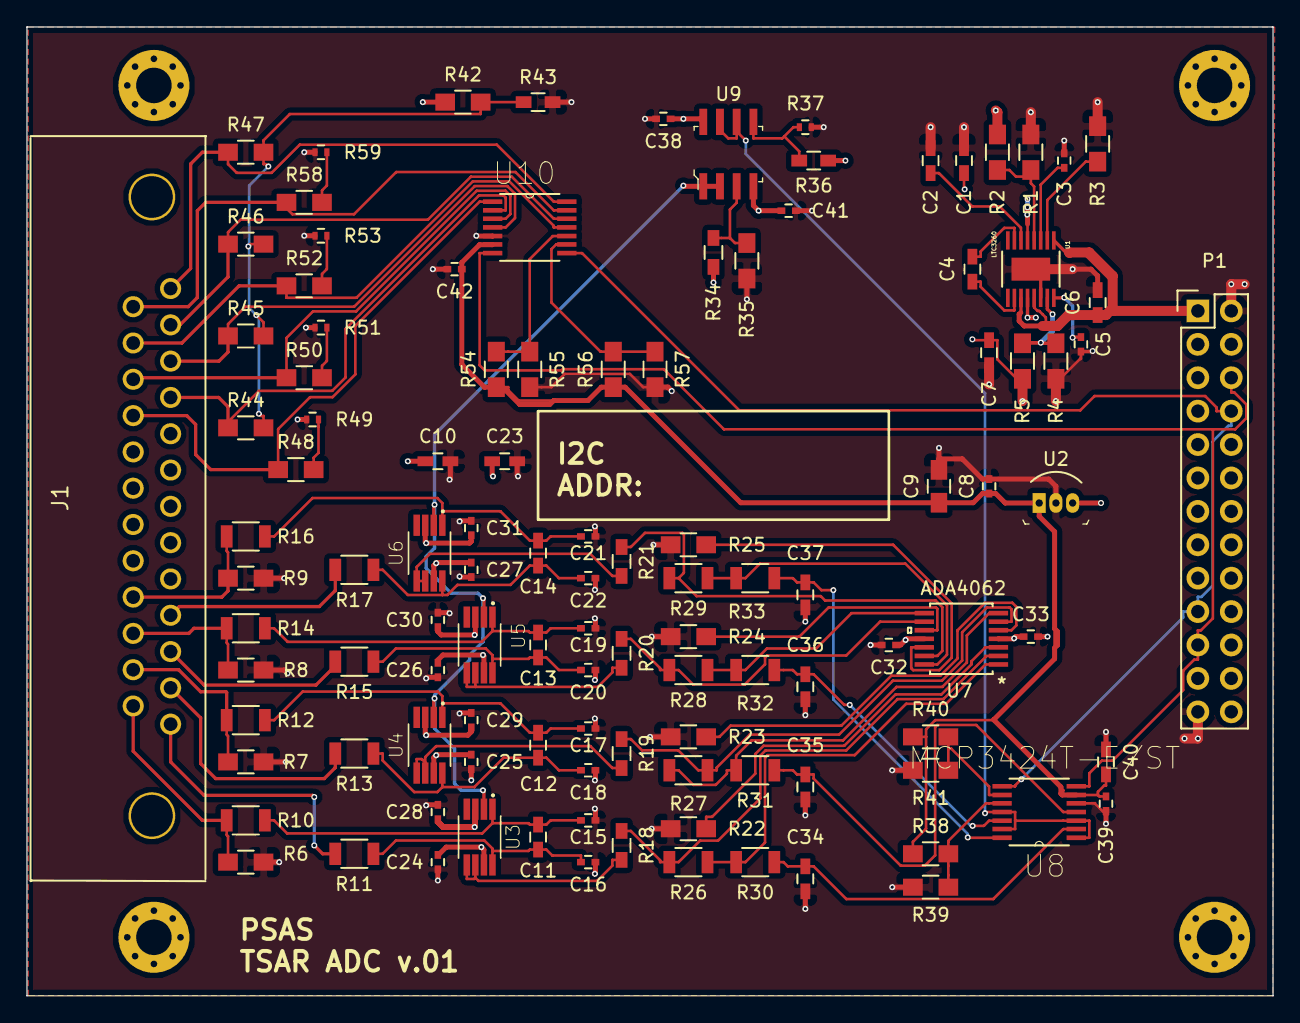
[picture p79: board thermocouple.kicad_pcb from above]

Board: 4 copper layers, 94.7 x 73.7 mm, 117 parts (0 on the bottom side), 72 nets.

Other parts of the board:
C38: .1uF; C_0402
R36: 11.1K; R_0603_HandSoldering
R37: 2.55K; R_0402
REF1, REF2, REF3, REF4: MountingHole_2.7mm_M2.5_Pad_Via

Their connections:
/power/+10V: C38.1, R36.1; also elsewhere on the board
unnamed 91: R36.2, R37.1; also elsewhere on the board

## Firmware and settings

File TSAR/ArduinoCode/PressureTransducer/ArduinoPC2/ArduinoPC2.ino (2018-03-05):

#include <Servo.h>

Servo myServo;
byte servoPin = 8;
byte servoMin = 10;
byte servoMax = 170;
byte servoPos = 0;
byte newServoPos = servoMin;

byte PTransducer1 = A1;
byte PTransducer2 = A3;
byte PTransducer3 = A4;
byte PTransducer4 = A5;
byte PTransducer5 = A6;
byte Thermocouple1 = A7;
byte Thermocouple2 = A8;

const byte numLEDs = 2;
byte ledPin[numLEDs] = {12, 13};
unsigned long LEDinterval[numLEDs] = {200, 400};
unsigned long prevLEDmillis[numLEDs] = {0, 0};

const byte buffSize = 40;
char inputBuffer[buffSize];
const char startMarker = '<';
const char endMarker = '>';
byte bytesRecvd = 0;
boolean readInProgress = false;
boolean newDataFromPC = false;

char messageFromPC[buffSize] = {0};
int newFlashInterval = 0;
float servoFraction = 0.0; // fraction of servo range to move


unsigned long curMillis;

unsigned long prevReplyToPCmillis = 0;
unsigned long replyToPCinterval = 1000;

//=============

void setup() {
  Serial.begin(9600);
  
    // flash LEDs so we know we are alive
  //for (byte n = 0; n < numLEDs; n++) {
  //   pinMode(ledPin[n], OUTPUT);
  //   digitalWrite(ledPin[n], HIGH);
  //}
  delay(500); // delay() is OK in setup as it only happens once
  
  //for (byte n = 0; n < numLEDs; n++) {
  //   digitalWrite(ledPin[n], LOW);
  //}
  
    // initialize the servo
  //myServo.attach(servoPin);
  //moveServo();
 Serial.println("<Arduino is ready>");
    // tell the PC we are ready
  if (strcmp(messageFromPC, "1") == 0) {
      Serial.println("<Arduino is ready>");
      delay(1000);
      ;
  }
}

//=============

void loop() {
  curMillis = millis();
  getDataFromPC();
  //moveServo();
  
  // make a string for assembling the data to log:
  String dataString = "";
    dataString += String(millis()/1000);
  // read eight sensors and append to the string:
  for (int analogPin = 3; analogPin < 16; analogPin++) {
    int sensor = analogRead(analogPin);
    dataString += String(sensor);
    //if (analogPin < 8) {
    dataString += ","; 
    //}
  }

  //updateFlashInterval(); //
  //updateServoPos();
  replyToPC(dataString);
  
  
}

//=============

void getDataFromPC() {

    // receive data from PC and save it into inputBuffer
    
  if(Serial.available() > 0) {

    char x = Serial.read();

      // the order of these IF clauses is significant
      
    if (x == endMarker) {
      readInProgress = false;
      newDataFromPC = true;
      inputBuffer[bytesRecvd] = 0;
      parseData();
    }
    
    if(readInProgress) {
      inputBuffer[bytesRecvd] = x;
      bytesRecvd ++;
      if (bytesRecvd == buffSize) {
        bytesRecvd = buffSize - 1;
      }
    }

    if (x == startMarker) { 
      bytesRecvd = 0; 
      readInProgress = true;
    }
  }
}

//=============
 
void parseData() {

    // split the data into its parts
    
  char * strtokIndx; // this is used by strtok() as an index
  
  strtokIndx = strtok(inputBuffer,",");      // get the first part - the string
  strcpy(messageFromPC, strtokIndx); // copy it to messageFromPC
  
  strtokIndx = strtok(NULL, ","); // this continues where the previous call left off
  newFlashInterval = atoi(strtokIndx);     // convert this part to an integer
  
  strtokIndx = strtok(NULL, ","); 
  servoFraction = atof(strtokIndx);     // convert this part to a float

}

//=============

void replyToPC( String update) {
  
//  if (True) {
    //newDataFromPC = false;
    Serial.print("<");
    Serial.print(update);
 //   Serial.print(" New Flash ");
 //   Serial.print(newFlashInterval);
 //   Serial.print(" SrvFrac ");
 //   Serial.print(servoFraction);
 //   Serial.print(" SrvPos ");
 //   Serial.print(newServoPos);
 //   Serial.print("Time");
 //   Serial.print(curMillis >> 9); // divide by 512 is approx = half-seconds
    Serial.println(">");
    delay(1500);
  //}
}

//============

void updateFlashInterval() {

   // this illustrates using different inputs to call different functions
  if (strcmp(messageFromPC, "LED1") == 0) {
     updateLED1();
  }
  
  if (strcmp(messageFromPC, "LED2") == 0) {
     updateLED2();
  }
}

//=============

void updateLED1() {

  if (newFlashInterval > 100) {
    LEDinterval[0] = newFlashInterval;
  }
}

//=============

void updateLED2() {

  if (newFlashInterval > 100) {
    LEDinterval[1] = newFlashInterval;
  }
}

//=============

void flashLEDs() {

  for (byte n = 0; n < numLEDs; n++) {
    if (curMillis - prevLEDmillis[n] >= LEDinterval[n]) {
       prevLEDmillis[n] += LEDinterval[n];
       digitalWrite( ledPin[n], ! digitalRead( ledPin[n]) );
    }
  }
}

//=============

//void updateServoPos() {

//  byte servoRange = servoMax - servoMin;
 // if (servoFraction >= 0 && servoFraction <= 1) {
   // newServoPos = servoMin + ((float) servoRange * servoFraction);
  //}
//}

//=============

//void moveServo() {
//  if (servoPos != newServoPos) {
 //   servoPos = newServoPos;
 //  myServo.write(servoPos);
//  }
//}

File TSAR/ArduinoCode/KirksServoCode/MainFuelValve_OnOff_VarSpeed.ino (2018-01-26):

/* Variable Speed Open and Close
 
Program actuates servo based on input from a switch or push button connected to digital pin 8. 

When switch is in off position, pin 8 is high, 
Servo moves to or remains at position = 0 at user defined speed

When switch is asserted, pin 8 is low,
Servo moves to position = 180 at user defined speed.

*/


#include <VarSpeedServo.h>

VarSpeedServo myservo;  // create servo object to control a servo
// twelve servo objects can be created on most boards
//Servo can operate at various speeds

int pos = 0;    // variable to store the servo position

 // pushbutton pin
 const int buttonPin = 8;

void setup() {
  myservo.attach(3);  // attaches the servo on pin 8 to the servo object
  pinMode(buttonPin, INPUT);
}

void loop() {
  int buttonState = digitalRead(buttonPin);

  if(!buttonState) //If switch is in "on", pin 8 is low, servo moves to 180 degrees; If switch is "off", pin 8 is high, servo returns to 0;
  {
    myservo.write(180, 90, true); //Parameters: (final pos, speed(varies from 1-255 slowest to fastest), won't move to next line of code until pos 180 is reached)
  }else{
    myservo.write(0, 90, true); 
  }
  delay(300);

}

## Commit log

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2016-09-09 Revert "Test Stand Assembly Updated"
    This reverts commit b79e00b5652df4786d6530549077c322bd3dee19.
    [4024T730_FIRE-TESTED STEEL BALL VALVE.SLDPRT, 4833K21_Mcmaster.SLDPRT, 50785K273_MED-PRESSURE BRASS THREADED PIPE FITTING.SLDPRT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]
2016-09-09 Revert "Revert "Test Stand Assembly Updated""
    This reverts commit b15a53cbb60ead466c05b91a562a29a795273f49.
    [4024T730_FIRE-TESTED STEEL BALL VALVE.SLDPRT, 4833K21_Mcmaster.SLDPRT, 50785K273_MED-PRESSURE BRASS THREADED PIPE FITTING.SLDPRT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]
2016-09-09 Revert "Revert "Revert "Test Stand Assembly Updated"""
    This reverts commit ef1ff43956c0bee73f7367af25b080eca4fa811c.
    [4024T730_FIRE-TESTED STEEL BALL VALVE.SLDPRT, 4833K21_Mcmaster.SLDPRT, 50785K273_MED-PRESSURE BRASS THREADED PIPE FITTING.SLDPRT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]
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2017-02-02 updated CAD files; fixed missing dependencies
    [4024T730_FIRE-TESTED STEEL BALL VALVE.SLDPRT, 46105K650_HIGH-PRESSURE COMPACT CHECK VALVE.SLDPRT, 4936K154_BSPT-BSPP-METRIC HI-PRESSURE STL THRD FITTING.SLDPRT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]
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2017-03-09 fixed a weird file name
    [equations-igniter6-v2.xlsx]
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2017-04-27 Update README.md
    Added preliminary project breakdown to read me and began linking current issues to it.
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2017-06-13 Created some solidworks models for main fuel valve prototype. added a couple spec sheets.
    [90473A210_LOW-STRENGTH STEEL HEX NUT.SLDPRT, Horn adapter.SLDPRT, Housing-Back.SLDPRT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]
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2017-07-10 Fixed encoding wheel logic and updated readme
    [12VDC_valve_assembly.SLDASM, encoding_wheel.SLDPRT]
2017-07-11 Updated: encoding wheel, motor & shaft split to two parts, valve added to assembly, mates fixed.
    [12VDC_valve_assembly.SLDASM, Motor_12VDC_638263.SLDPRT, encoding_wheel.SLDPRT]
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2017-07-11 07.10.2017 added hardware and fixed LED pattern drawing (over-defined)
    [90128A125_ZNC-PLTD ALLOY STL SCKT HEAD CAP SCREW.SLDPRT, 92562A122_MIL SPEC ALLOY STEEL SOCKET HEAD CAP SCREW.SLDPRT, 92562A125_MIL SPEC ALLOY STEEL SOCKET HEA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]
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2017-08-06 Updated 12VDC housing and assembly to final for printing. Added housing back and front.
    [12VDC_valve_assembly.SLDASM, 545576_assembly.SLDASM, 555174_assembly.SLDASM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]
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2017-09-20 Moved igniter resources to a separate folder and added a jupyter notebook to begin calculations.
    [BW-High-Pres_Eth.xls, BW-High-Pres_Eth_2.xls, BW_Low-Pres_Eth.xls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]
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2017-11-23 Fixed 12VDC MFV assembly
    [12VDC_valve_assembly.SLDASM, Housing_01.SLDASM, LED_Head.SLDPRT]
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2018-01-24 Created modified fuel tank top plate for machining. Place in new cad folder.
    [fuel_top_plate.SLDPRT]
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2018-09-05 Add files via upload
    Initial version of Kicad design for TSAR ADC board.
    [TSAR_ADC_Board_BOM.csv, power.sch, pressure_ckt.sch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]
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2019-01-15 Adding Data From First Calibration Tests
    Flow and pressure calibration data added. Also some changes to the pintle test das.
    [100psi.xlsx, 120psi.xlsx, 37psi.xlsx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]
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2019-04-02 New AN fittings added
    New AN fittings added to CAD folder with preliminary LOX side pressure panel fittings added on test stand CAD
    [0306_08_AL.sldprt, 0306_08_SS.sldprt, 238754-500.sldprt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]
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2019-04-10 CAD fittings update
    More fittings added, all sections complete. Added flared tube end. Beginning piping.
    [90 degree pipe bend.SLDPRT, Flared pipe end - .25 inch.SLDPRT, Flared pipe end - .5 inch - Copy (10).SLDPRT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]
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2019-04-13 CAD piping update
    Preliminary pipes for lower LOX and lower fuel side added
    [Flared pipe end - .5 inch.SLDPRT, Fuel Top plate.SLDPRT, LOX Top plate.SLDPRT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]
2019-04-15 CAD Preliminary Piping
    All piping for available sections added and is ready for review.
    [Pipe 16.sldprt, Assem1.sldasm, Assem3.sldasm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]
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2019-04-23 Integrated new igniter system
    New igniter system added to main test stand CAD
    [.25 inch Venturi meter.SLDPRT, FuelOxy Bottle.SLDPRT, Igniter Arm 1st Section.SLDPRT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]
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2019-04-25 Updated test stand CAD
    Updated venturi CAD and added pintle V2 CAD to main test stand assembly
    [.25 inch Venturi meter.SLDPRT]
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2019-05-02 test stand CAD update
    Real venturis added to main test stand CAD. Begining piping
    [.25 inch Venturi meter.SLDPRT, .5 inch straight tube.SLDPRT, .5 inch venturi.SLDPRT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]
2019-05-03 main test stand CAD update
    all piping until bulkhead has been completed.
    [Pipe 16.sldprt, AL-5000-08-08.SLDPRT, AN826-8D.SLDPRT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]
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2019-05-07 CAD piping update
    adjustments made to intial straight lengths of pipes to account for fitting assembly
    [Copy of Part1.sldprt, Copy of Part2.SLDPRT, Part1.sldprt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]
2019-05-09 CAD piping update
    All piping up to bulkheads completed along with drawings to send out for manufacturing
    [Copy of Part2.SLDPRT, Copy of Pipe Sketch.sldprt, Part10.SLDPRT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]
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2019-05-14 Updated LOX valves and pipes
    Updated placeholder LOX valves to ones we currently have. Updated piping to make room for LOX valves. Updated drawings for stainless steel piping to be sent for manufacturing.
    [Copy of Part2.SLDPRT, LOX valve.SLDPRT, Part12.SLDPRT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]
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2019-05-16 Piping and order update
    Updated LOX side piping to account for manufacturing procedures along with updating the drawings to be sent out for manufacturing.
    [Pipe 16.sldprt, .5 inch straight tube.SLDPRT, .5 inch venturi.SLDPRT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]
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2019-05-22 updates to the Pintle design documents and initial raw data from pintle V3 hydro testing
    [100psiannulus1.xls, 100psiannulus2.xls, 100psiannulus3.xls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]
2019-05-23 CAD update
    Update to LOX side pipes with the addition of new fittings. Revised format for pipe drawings also.
    [5482K340_PRECISION AN 37 DEGREE FLARED TUBE FITTING.SLDPRT, Pipe 10.SLDDRW, Pipe 11.SLDDRW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]
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2019-05-28 CAD preliminary final version
    Updated fittings, added nuts and sleeves, adjusted some piping
    [.5 inch straight tube.SLDPRT, 0.5in standoff.SLDPRT, 535110 assembly - Pillow.SLDASM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]
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2019-05-29 testing equation display fix on documentation
    [flow rate graph.xlsx]
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2020-01-29 Work on test stand assembly
    + adding in more valves, mocked up an actuated valve
    [3310T530_STRUT CHANNEL_2ft.SLDPRT, 3310T530_STRUT CHANNEL_33.75.SLDPRT, Assembly_LFETS.SLDASM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]
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2020-04-17 tubing drawing demo
    made some demo tubing files . go ahead and delete them later
    [demoTube.SLDDRW, demoTube.sldprt, tubeDemo2.SLDDRW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]
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2020-05-02 routing_tutorial_part_deux
    things to do:
    create tubing templates (.5 OD and .75 OD)
    [0500_OD_JIC_to_0500_NPT.SLDPRT, 3Tube-500X020.SLDDRW, 3Tube-500X020.sldprt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]
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2020-05-07 LOX fill tubing
    added tubing, fittings, and valves for the LOX fill side of the test stand.
    the flange on the bottom is a place holder for a more attractive interface with the LOX dewar
    [2698K160_ULTRA-CORROSION-RESISTANT THRDED PIPE FITTING.SLDPRT, 49415K320_CLEANED AND BAGGED CRYOGENIC GLOBE VALVE.SLDPRT, CG500B_w_fittings.SLDASM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]
2020-05-07 fixed some crap, broke some crap
    too many questions... for 5/7 meeting
    [4443K645_HIGH-PRESSURE 316 SS THREADED PIPE FITTING.SLDPRT, 4464K642_TYPE 304 STAINLESS STL THREADED PIPE FITTING.SLDPRT, 45525K555_HIGH-PRESSURE 304 SS THREAD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]
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2020-07-15 Load Cell Replacment
    Makeshift load cell blocks were replaced with spacers for the new FC23 load cell. Bolts to attach FC23 to spacers are missing, parts left floating to indicate the bolt holes are unfinished.
    [load_cell_2020_spacer.SLDPRT, load_cell_assembly_R2_2020_new.SLDASM]
2020-07-28 Finished redesign of load cell assembly
    Finished redesign of load cell assembly to accomodate the new FC23 load cells.
    [92196A846_18-8 STAINLESS STEEL SOCKET HEAD SCREW.SLDPRT, Part1.sldprt, Part2.sldprt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]
2020-08-04 FC 23 Load Cell Addition + Spacer
    Finished dummy modelling of spacer for the new load cell, some dimensions are just place holders for now. The shoulder bolts in the thrust plate were replaced.
    [Tube_5-Assembly_LFETS-001.sldasm, load_cell.sldasm, load_cell_2020_spacer.SLDPRT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]
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

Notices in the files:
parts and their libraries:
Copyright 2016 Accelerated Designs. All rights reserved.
